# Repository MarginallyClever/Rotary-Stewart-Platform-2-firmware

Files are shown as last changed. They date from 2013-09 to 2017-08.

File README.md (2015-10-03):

#RotaryStewartPlatform2

a 6-axis motion control platform for scientists, students, and enthusiasts.

This project contains the firmware that lives in the brain of a RUMBA board, an Arduino-compatible 6 stepper driver.

This robot is easily controlled from Evil Overlord (https://github.com/i-make-robots/Evil-Overlord), a 3D simulator for Marginally Clever robots.

##Get it

Buy one today at http://www.marginallyclever.com/shop/index.php?main_page=product_info&cPath=1&products_id=74

##Put it together

Our helpful website has all the explanation and pictures to guide you along.
http://learn.marginallyclever.com/index.php/Stewart_Platform_2

##Help!

For technical assistance please visit our forums at https://marginallyclever.com/forums

##More

This code is online @ http://www.github.com/MarginallyClever/RotaryStewartPlatform2

##Author

http://marginallyclever.com
Dan Royer
2013-09-18

This document last updated 2015-10-03

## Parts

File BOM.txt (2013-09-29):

Bill of Materials 2013-09-16 Adafruit Shields
---------------------------------------------
1x Arduino
3x Adafruit Motor Shield v2
6x NEMA17 400 steps per turn
1x USB cable, A to B, 1.5m
1x 12v2a power supply
3x Power cable, 5.5x2.1 1 female to 3 male 
1x Power cable, 5.5x2.1 female
6x micro switches
1x set laser cut parts
6x M3x105 threaded rod
6x M3x5 pan phillips screw
18x M3x15 pan phillips screws
18x M3 hex nuts
12x Traxxas ball joints
10x 2x60 zip ties 

Bill of Materials 2013-09-20 RUMBA shields
---------------------------------------------
1x RUMBA controller
6x NEMA17 400 steps per turn
1x USB cable, A to mini, 1.5m
1x 12v2a power supply
1x Power cable, 5.5x2.1 female
6x micro switches
1x set laser cut parts
6x M3x105 threaded rod
6x M3x5 pan phillips screw
18x M3x15 pan phillips screws
18x M3 hex nuts
12x Traxxas ball joints
10x 2x60 zip ties

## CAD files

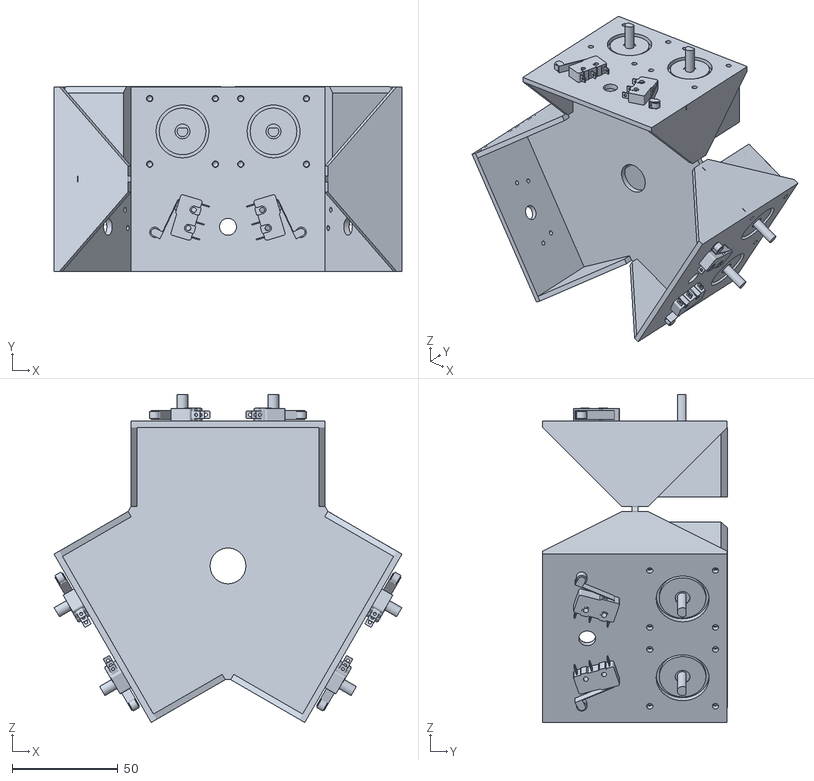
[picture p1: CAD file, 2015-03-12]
base.STL
164.3 x 87.3 x 154.9

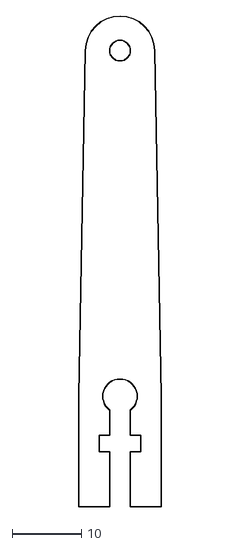
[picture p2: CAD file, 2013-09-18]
DXF files/arm-a.DXF
12.0 x 71.0

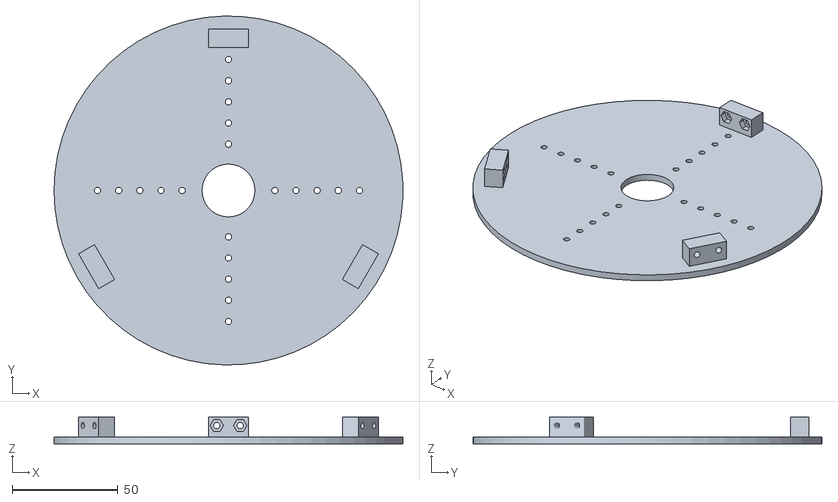
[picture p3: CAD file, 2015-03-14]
STL files/top.STL
165.0 x 164.9 x 12.7

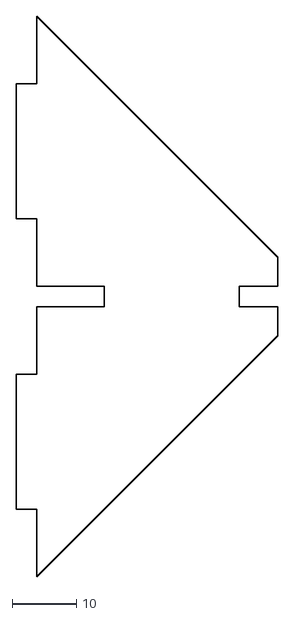
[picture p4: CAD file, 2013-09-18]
DXF files/motor-face-b.DXF
40.7 x 87.2

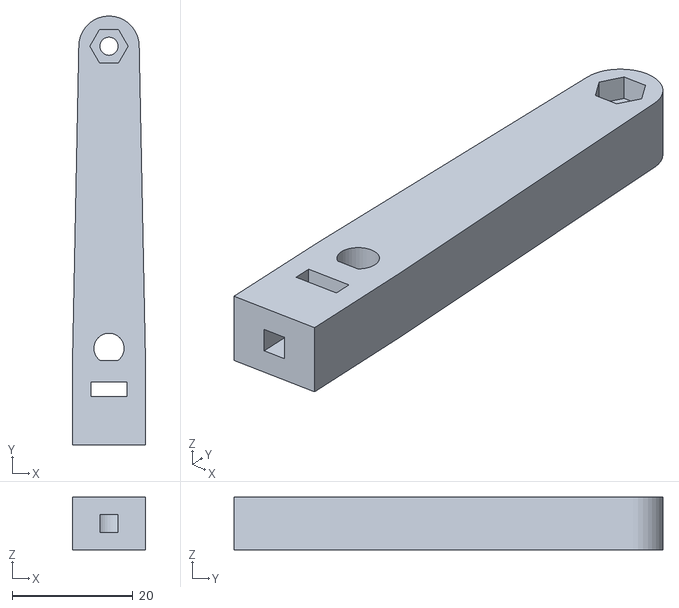
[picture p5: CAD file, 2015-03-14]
STL files/arm.STL
12.0 x 71.0 x 8.70

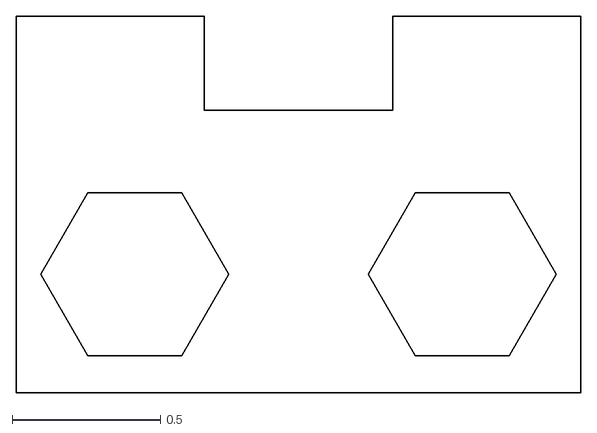
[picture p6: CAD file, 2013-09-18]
DXF files/top-tab-b.DXF
1.91 x 1.27

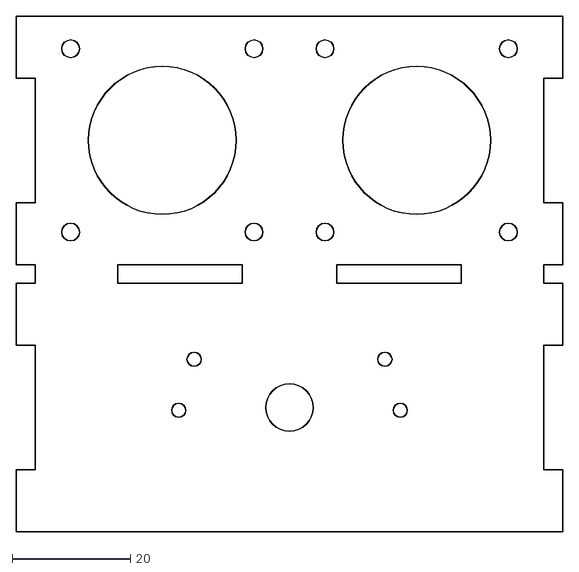
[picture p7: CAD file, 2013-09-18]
DXF files/motor-face-a.DXF
92.3 x 87.2

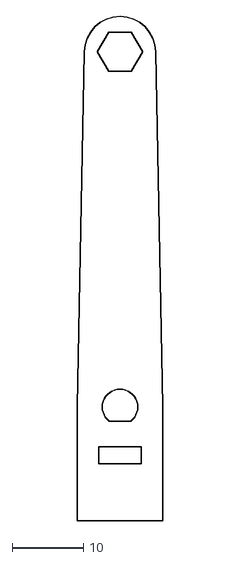
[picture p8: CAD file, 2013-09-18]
DXF files/arm-c.DXF
12.0 x 71.0

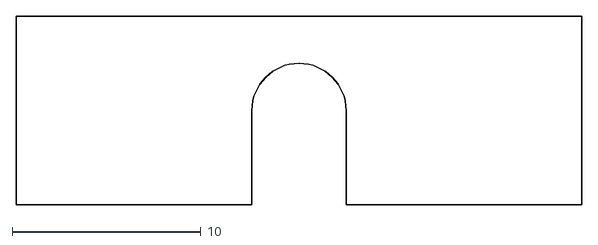
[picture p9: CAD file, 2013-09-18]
DXF files/spacer.DXF
30.0 x 10.0

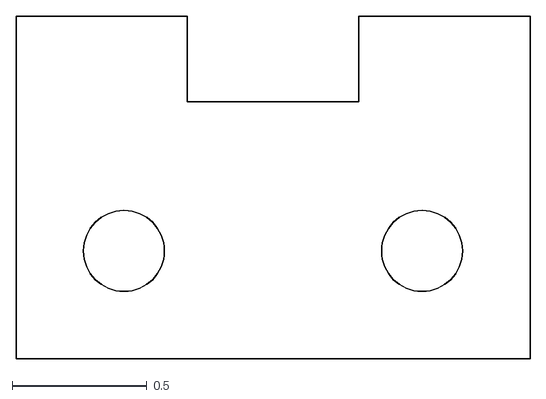
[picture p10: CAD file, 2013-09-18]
DXF files/top-tab-a.DXF
1.91 x 1.27

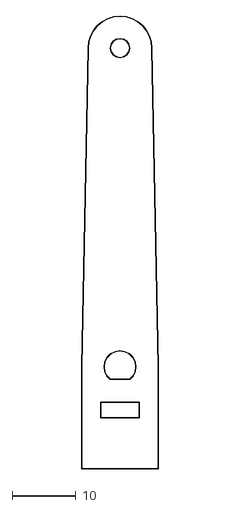
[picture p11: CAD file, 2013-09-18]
DXF files/arm-b.DXF
12.0 x 71.0

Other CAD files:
DXF files/base.DXF
DXF files/top.DXF

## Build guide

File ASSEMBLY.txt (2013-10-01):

Stewart Platform Assembly
---------------------------
Introduction
Glueing
The switches
The stepper motors
The arms
The stewart platform
Final tests

---------------------------
Introduction
	tools you will need
	  	- soldering iron
	  	- Arduino software
	  	- small Phillips screwdriver
	  	- crazy glue
	  	- masking tape
      - pliers
	open and inspect your kit
		IMG_5941
	  	compare with the BOM to make sure everything arrived in working order.
  		We have checked contents before shipping.
      
---------------------------
Glueing
	the frame
		IMG_5944-IMG_5947
	the top
		IMG_5948,49,58-63
	the biceps
		IMG_5950-57
		This is the hardest part!  Make sure the pieces line up correctly.
		Once the glue has dried an M3x15 goes in the hole at the square end and is held in place with an M3 nut.
    
---------------------------
The switches
	soldering
		<picture missing>
		red is the pin closest to the roller.
		black is the center pin.
		blue is the pin closest to the clicker.
	test
		<picture of soldering>
		connect the RUMBA controller to your computer with the USB cable provided.
		<picture of RUMBA input pins>
		connect the switch to an input.
		install test_switches.ino
		open the serial window and set the baud rate to 57600.
		press the switch.  A column should change from 1 to 0.
		disconnect USB.
	install
		thread the wire for two switches through the hole in each face.  secure the switches with zip ties so that the roller is downward.
			<picture>
			Switches 1 and 2 should be side-by-side.
			Switches 3 and 4 should be side-by-side.
			Switches 5 and 6 should be side-by-side.
	test 2
		connect the RUMBA controller to your computer with the USB cable provided.
		the switches again to be sure they are in the correct order.
		disconnect USB.
    
---------------------------
The stepper motors
	attach
		<picture of wiring for stepper 0>
		the wires order from left to right should be red, green, blue, yellow.
		connect the 5.1x2.2 female power supply to the RUMBA
	test one
		connect the 12v2a power supply to the RUMBA.
		install test_steppers_rumba.ino.  Motors will begin to move as soon as sketch uploads.
		open the serial window to see what the code is doing.
		when the test works, remove the stepper from the Arduino.
		disconnect 12v power and USB.
	install
		<picture of tape with writing>
		put a piece of tape on each stepper and at the far end of the wire.
		write the stepper number on the appropriate tape.
		<picture of steppers installed>
		install the steppers in a clockwise order.
			Steppers 1 and 2 should be side-by-side.
			Stepper 1 should be above switch 1.
			Stepper 2 should be above switch 2.
			Repeat for steppers 3-6.
		put the wires through the hole in the center of the frame.
		attach the steppers in order with M3x5 screws.
			The tape will make it easy to keep them organized.
	test 
		Make sure 12v power is not connected.
		put a small piece of tape on each motor shaft so you can easily see it move.
		install firmware_rumba_minimal.ino
		open the serial window.
			G00 X100; should turn stepper 1.
			G00 Y100; should turn stepper 2 *in the opposite direction*.
			G00 Z100; should turn stepper 3 same direction as #1.
			G00 U100; should turn stepper 4 same direction as #2.
			G00 V100; should turn stepper 5 same direction as #1.
			G00 W100; should turn stepper 6 same direction as #2.
      
---------------------------
The arms
  assemble the forearms: One ball joint goes on the end of each threaded rod.
    There should be ~140mm of visible rod between the two ball joints.
    The distance from center hole to center hole should be 167.5mm.
    The holes on the rods should be aligned.
    Use a small pair of pliers to press the metal ball into the plastic frame.
	attach the biceps to the forearms
		<picture of biceps and forearms>
	attach the forearms to the top
		<picture of forearms and top>
		make sure the arms are attached on the correct side. 
	attach the biceps to the motor shafts
		IMG_5964-66
		use the spacer to make sure the biceps are at the correct distance from the frame.
		make sure the biceps are facing the correct direction.
		make sure the biceps touch the limit switches.
    
---------------------------
The stewart platform
	Make sure 12v power is not connected.
	install firmware_rumba_minimal.ino
	open the serial window.
	Connect 12v power.
  
---------------------------
Final tests
	M18; disables power to all stepper motors.
		You can freely move the platform.  Don't forget gravity is in effect!
	M17; enables power to all stepper motors.
		Try manually holding the platform at a strange angle and enabling power.
	Test short movements on each stepper motor.
		M18;
		move the platform so each bicep is approximately level.
		M17;
		Be prepared to disconnect 12v power if something goes wrong.
		G00 F200 Z1; should slowly move the platform up one centimeter.
	test homing
		G28;
		Steppers should immediately move "down" to touch switches and then move to home position.
		Because of the previous F200 they will move slowly.
	test full speed
		G00 F800; changes speed without moving.
		G00 X1.5; should move 15mm sideways.
		G00 Y1.5; should move 15mm orthogonal to X and Z.
		G00 U10; tilt 10 degrees around Y.
		G00 V-8.25; tilt 8.25 degrees around X.
		G00 W5; twist 5 degrees around Z.
		G00 X0 Y0 Z0 U0 V0 W0; will move back to center, flat.
		
Congratulations!  Your platform is assembled and appears to be working.

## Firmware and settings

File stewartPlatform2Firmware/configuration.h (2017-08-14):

#ifndef CONFIGURATION_H
#define CONFIGURATION_H
//------------------------------------------------------------------------------
// Stewart Platform v2 - Supports RUMBA 6-axis motor shield
// dan@marginallycelver.com 2013-09-20
//------------------------------------------------------------------------------
// Copyright at end of file.
// please see http://www.github.com/MarginallyClever/RotaryStewartPlatform2 for more information.


//------------------------------------------------------------------------------
// CONSTANTS
//------------------------------------------------------------------------------
#define VERBOSE              (0)  // increase this number to get more output
#define DEBUG_SWITCHES       (0)

// uncomment this line to test stepper motor wiring
//#define TEST_STEPPERS

// Comms
#define BAUD                 (57600)  // How fast is the Arduino talking?
#define MAX_BUF              (64)  // What is the longest message we can store?

// Stepper motors
#define STEPS_PER_TURN       (400)  // depends on your stepper motor.  most are 200.
#define MICROSTEPS           (16.0)
#define MICROSTEPS_PER_TURN  (STEPS_PER_TURN*MICROSTEPS)
#define MICROSTEP_PER_DEGREE (MICROSTEPS_PER_TURN/360.0)

// speed and acceleration
#define MAX_FEEDRATE         (9000.0)  // depends on timer interrupt & hardware
#define MIN_FEEDRATE         (1.0)
#define DEFAULT_FEEDRATE     (5000.0)
#define DEFAULT_ACCELERATION (3000.0)

#define MIN_STEP_DELAY       (50)  // used for stepper test

// misc
#define NUM_AXIES            (6)

// related to number of instructions that can be buffered.  must be a power of two > 1.
#define MAX_SEGMENTS         (32)  // must be a power of 2
// for splitting lines and look-ahead
#define MM_PER_SEGMENT       (3)

// convenience macros
#define TWOPI                (PI*2.0)
#define DEG2RAD              (PI/180.0)
#define RAD2DEG              (180.0/PI)



//------------------------------------------------------------------------------
// TIMER 
//------------------------------------------------------------------------------
// time passed with no instruction?  Make sure PC knows we are waiting.
#define TIMEOUT_OK           (1000)
// timing
#define CLOCK_FREQ           (16000000L)
#define MAX_COUNTER          (65536L)


// optimize code, please
#define FORCE_INLINE         __attribute__((always_inline)) inline

#ifndef CRITICAL_SECTION_START
  #define CRITICAL_SECTION_START  unsigned char _sreg = SREG;  cli();
  #define CRITICAL_SECTION_END    SREG = _sreg;
#endif //CRITICAL_SECTION_START



//------------------------------------------------------------------------------
// hardware/software pins
//------------------------------------------------------------------------------
#define MOTOR_0_DIR_PIN    (16)
#define MOTOR_0_STEP_PIN   (17)
#define MOTOR_0_ENABLE_PIN (48)
#define MOTOR_0_LIMIT_PIN  (37)

#define MOTOR_1_DIR_PIN    (47)
#define MOTOR_1_STEP_PIN   (54)
#define MOTOR_1_ENABLE_PIN (55)
#define MOTOR_1_LIMIT_PIN  (36)

#define MOTOR_2_DIR_PIN    (56)
#define MOTOR_2_STEP_PIN   (57)
#define MOTOR_2_ENABLE_PIN (62)
#define MOTOR_2_LIMIT_PIN  (35)

#define MOTOR_3_DIR_PIN    (22)
#define MOTOR_3_STEP_PIN   (23)
#define MOTOR_3_ENABLE_PIN (27)
#define MOTOR_3_LIMIT_PIN  (34)

#define MOTOR_4_DIR_PIN    (25)
#define MOTOR_4_STEP_PIN   (26)
#define MOTOR_4_ENABLE_PIN (24)
#define MOTOR_4_LIMIT_PIN  (33)

#define MOTOR_5_DIR_PIN    (28)
#define MOTOR_5_STEP_PIN   (29)
#define MOTOR_5_ENABLE_PIN (39)
#define MOTOR_5_LIMIT_PIN  (32)


//------------------------------------------------------------------------------
// EEPROM MEMORY MAP
//------------------------------------------------------------------------------
#define EEPROM_VERSION   2                         // Increment EEPROM_VERSION when adding new variables

#define ADDR_VERSION     0                         // address of the version number (one byte)
#define ADDR_GUID        (ADDR_VERSION+1)          // address of the UUID (long - 4 bytes)

// sensor adjustments
#define ADDR_ANGLE1      (ADDR_GUID  +4)
#define ADDR_ANGLE2      (ADDR_ANGLE1+4)
#define ADDR_ANGLE3      (ADDR_ANGLE2+4)
#define ADDR_ANGLE4      (ADDR_ANGLE3+4)
#define ADDR_ANGLE5      (ADDR_ANGLE4+4)
#define ADDR_ANGLE6      (ADDR_ANGLE5+4)


//------------------------------------------------------------------------------
// GLOBALS
//------------------------------------------------------------------------------
extern long robot_uid;


/**
* This file is part of Stewart Platform v2.
*
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
re details.
*
* You should have received a copy of the GNU General Public License
* along with Stewart Platform v2. If not, see <http://www.gnu.org/licenses/>.
*/
#endif

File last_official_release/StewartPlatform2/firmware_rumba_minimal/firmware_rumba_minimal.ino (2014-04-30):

//------------------------------------------------------------------------------
// Stewart Platform v2 - Supports Adafruit motor shield v2
// dan@marginallycelver.com 2013-09-07
//------------------------------------------------------------------------------
// Copyright at end of file.
// please see http://www.github.com/MarginallyClever/RotaryStewartPlatform2 for more information.

/**
 * top center to wrist hole: X76.35 Y+/-5.53 Z8.7
 * base center to shoulder hole: X80.93 Y+/-21.5 Z78.31
 */

//------------------------------------------------------------------------------
// CONSTANTS
//------------------------------------------------------------------------------
//#define VERBOSE              (1)  // add to get a lot more serial output.
//#define DEBUG_SWITCHES       (1)

#define VERSION              (1)  // firmware version
#define BAUD                 (57600)  // How fast is the Arduino talking?
#define MAX_BUF              (64)  // What is the longest message Arduino can store?
#define STEPS_PER_TURN       (400)  // depends on your stepper motor.  most are 200.
#define MIN_STEP_DELAY       (100)
#define MAX_FEEDRATE         (1000000/MIN_STEP_DELAY)
#define MIN_FEEDRATE         (0.01)
#define NUM_AXIES            (6)
#define MICROSTEP_MUL        (16.0)

// measurements based on computer model of robot
#define BICEP_LENGTH         (5.01)
#define FOREARM_LENGTH       (16.75)
#define CIRCUMFERENCE        (BICEP_LENGTH*PI*2.0)
#define STEP_DISTANCE        ((CIRCUMFERENCE/MICROSTEP_MUL)/STEPS_PER_TURN)


//------------------------------------------------------------------------------
// INCLUDES
//------------------------------------------------------------------------------


//------------------------------------------------------------------------------
// STRUCTS
//------------------------------------------------------------------------------
// for line()
typedef struct {
  long delta;
  long absdelta;
  int dir;
  long over;
} Axis;


typedef struct {
  int motor_step_pin;
  int motor_dir_pin;
  int motor_enable_pin;
  int motor_scale;  // 1 or -1
  int limit_switch_pin;
  int limit_switch_state;  
} Arm;


//------------------------------------------------------------------------------
// GLOBALS
//------------------------------------------------------------------------------
Arm arms[NUM_AXIES];

Axis a[NUM_AXIES];  // for line()
Axis atemp;  // for line()

char buffer[MAX_BUF];  // where we store the message until we get a ';'
int sofar;  // how much is in the buffer

// speeds
float fr=0;  // human version
long step_delay;  // machine version
int step_delay_s;
int step_delay_us;

float px,py,pz,pu,pv,pw;  // position

// settings
char mode_abs=1;  // absolute mode?

#ifdef VERBOSE
char *letter="UVWXYZ";
#endif


//------------------------------------------------------------------------------
// METHODS
//------------------------------------------------------------------------------


/**
 * delay for the appropriate number of microseconds
 * @input ms how many milliseconds to wait
 */
void pause(long ms) {
  delay( step_delay_s );
  delayMicroseconds( step_delay_us );  // delayMicroseconds doesn't work for ms values > ~16k.
}


/**
 * Set the feedrate (speed motors will move)
 * @input nfr the new speed in steps/second
 */
void feedrate(float nfr) {
  if(fr==nfr) return;  // same as last time?  quit now.

  if(nfr>MAX_FEEDRATE) {
    Serial.print(F("New feedrate must be less than "));
    Serial.print(MAX_FEEDRATE);
    Serial.println(F("steps/s."));
    nfr=MAX_FEEDRATE;
  }
  if(nfr<MIN_FEEDRATE) {  // don't allow crazy feed rates
    Serial.print(F("New feedrate must be greater than "));
    Serial.print(MIN_FEEDRATE);
    Serial.println(F("steps/s."));
    nfr=MIN_FEEDRATE;
  }
  step_delay = 1000000.0/nfr;
  step_delay_s  = step_delay / 1000;
  step_delay_us = step_delay % 1000;
  fr=nfr;
}


/**
 * Set the logical position
 * @input npx new position x
 * @input npy new position y
 */
void position(float npx,float npy,float npz,float npu,float npv,float npw) {
  // here is a good place to add sanity tests
  px=npx;
  py=npy;
  pz=npz;
  pu=npu;
  pv=npv;
  pw=npw;
}


/**
 * Move one motor in a given direction
 * @input the motor number [0...6]
 * @input the direction to move 1 for forward, -1 for backward
 **/
void onestep(int motor,int dir) {
#ifdef VERBOSE
  Serial.print(letter[motor]);
#endif
  dir *= arms[motor].motor_scale;
  digitalWrite(arms[motor].motor_dir_pin,dir>0?LOW:HIGH);
  digitalWrite(arms[motor].motor_step_pin,LOW);
  digitalWrite(arms[motor].motor_step_pin,HIGH);
}


/**
 * Grips the power on the motors
 **/
void motor_enable() {
  int i;
  for(i=0;i<NUM_AXIES;++i) {
    digitalWrite(arms[i].motor_enable_pin,LOW);
  }
}


/**
 * Releases the power on the motors
 **/
void motor_disable() {
  int i;
  for(i=0;i<NUM_AXIES;++i) {
    digitalWrite(arms[i].motor_enable_pin,HIGH);
  }
}


/**
 * Uses bresenham's line algorithm to move both motors
 * @input newx the destination x position
 * @input newy the destination y position
 **/
void line(float newx,float newy,float newz,float newu,float newv,float neww) {
  a[0].delta = newx-px;
  a[1].delta = newy-py;
  a[2].delta = newz-pz;
  a[3].delta = newu-pu;
  a[4].delta = newv-pv;
  a[5].delta = neww-pw;
  
  long i,j,maxsteps=0;

  for(i=0;i<NUM_AXIES;++i) {
    a[i].dir = (a[i].delta > 0 ? 1:-1);
    a[i].absdelta = abs(a[i].delta);
    a[i].over=0;
    if(maxsteps<a[i].absdelta) maxsteps=a[i].absdelta;
  }
  
#ifdef VERBOSE
  Serial.println(F("Start >"));
#endif
  
  for(i=0;i<maxsteps;++i) {
    for(j=1;j<NUM_AXIES;++j) {
      a[j].over += a[j].absdelta;
      if(a[j].over >= maxsteps) {
        a[j].over -= maxsteps;
        onestep(j,a[j].dir);
      }
    }
    pause(step_delay);
  }

#ifdef VERBOSE
  Serial.println(F("< Done."));
#endif

  // This does not take into account movements of a fraction of a step.  They will be misreported and lead to error.
  position(newx,newy,newz,newu,newv,neww);
}


/**
 * Look for character /code/ in the buffer and read the float that immediately follows it.
 * @return the value found.  If nothing is found, /val/ is returned.
 * @input code the character to look for.
 * @input val the return value if /code/ is not found.
 **/
float parsenumber(char code,float val) {
  char *ptr=buffer;
  while(ptr && *ptr && ptr<buffer+sofar) {
    if(*ptr==code) {
      return atof(ptr+1);
    }
    ptr=strchr(ptr,' ')+1;
  }
  return val;
} 


/**
 * write a string followed by a float to the serial line.  Convenient for debugging.
 * @input code the string.
 * @input val the float.
 */
void output(char *code,float val) {
  Serial.print(code);
  Serial.println(val);
}


/**
 * print the current position, feedrate, and absolute mode.
 */
void where() {
  output("X",px);
  output("Y",py);
  output("Z",pz);
  output("U",pu);
  output("V",pv);
  output("W",pw);
  output("F",fr);
  Serial.println(mode_abs?"ABS":"REL");
} 


/**
 * display helpful information
 */
void help() {
  Serial.print(F("StewartPlatform v4-2"));
  Serial.println(VERSION);
  Serial.println(F("Commands:"));
  Serial.println(F("M17/M18; - enable/disable motors"));
  Serial.println(F("M100; - this help message"));
  Serial.println(F("M114; - report position and feedrate"));
  Serial.println(F("F, G00, G01, G04, G17, G18, G28, G90, G91, G92 as described by http://en.wikipedia.org/wiki/G-code"));
}


/**
 * Read the input buffer and find any recognized commands.  One G or M command per line.
 */
void processCommand() {
  int cmd = parsenumber('G',-1);
  switch(cmd) {
  case  0: // move linear
  case  1: // move linear
    feedrate(parsenumber('F',fr));
    line( parsenumber('X',(mode_abs?px:0)) + (mode_abs?0:px),
          parsenumber('Y',(mode_abs?py:0)) + (mode_abs?0:py),
          parsenumber('Z',(mode_abs?pz:0)) + (mode_abs?0:pz),
          parsenumber('U',(mode_abs?pu:0)) + (mode_abs?0:pu),
          parsenumber('V',(mode_abs?pv:0)) + (mode_abs?0:pv),
          parsenumber('W',(mode_abs?pw:0)) + (mode_abs?0:pw) );
    break;
  case  4:  pause(parsenumber('P',0)*1000);  break;  // dwell
  case 28:  find_home();  break;  
  case 90:  mode_abs=1;  break;  // absolute mode
  case 91:  mode_abs=0;  break;  // relative mode
  case 92:  // set logical position
    position( parsenumber('X',0),
              parsenumber('Y',0),
              parsenumber('Z',0),
              parsenumber('U',0),
              parsenumber('V',0),
              parsenumber('W',0) );
    break;
  default:  break;
  }

  cmd = parsenumber('M',-1);
  switch(cmd) {
  case 17:  motor_enable();  break;
  case 18:  motor_disable();  break;
  case 100:  help();  break;
  case 114:  where();  break;
  default:  break;
  }
}


/**
 * prepares the input buffer to receive a new message and tells the serial connected device it is ready for more.
 */
void ready() {
  sofar=0;  // clear input buffer
  Serial.print(F(">"));  // signal ready to receive input
}


/**
 * read the limit switch states
 * @return 1 if a switch is being hit
 */
char read_switches() {
  char i, hit=0;
  int state;
  
  for(i=0;i<6;++i) {
    state=digitalRead(arms[i].limit_switch_pin);
#ifdef DEBUG_SWITCHES
    Serial.print(state);
    Serial.print('\t');
#endif
    if(arms[i].limit_switch_state != state) {
      arms[i].limit_switch_state = state;
#ifdef DEBUG_SWITCHES
      Serial.print(F("Switch "));
      Serial.println(i,DEC);
#endif
    }
    if(state == LOW) ++hit;
  }
#ifdef DEBUG_SWITCHES
  Serial.print('\n');
#endif
  return hit;
}


/**
 * setup the limit switches
 */
void setup_switches() {
  arms[0].limit_switch_pin=37;
  arms[1].limit_switch_pin=36;
  arms[2].limit_switch_pin=35;
  arms[3].limit_switch_pin=34;
  arms[4].limit_switch_pin=33;
  arms[5].limit_switch_pin=32;
  
  for(int i=0;i<NUM_AXIES;++i) {  
    // set the switch pin
    arms[i].limit_switch_state=HIGH;
    pinMode(arms[i].limit_switch_pin,INPUT);
    digitalWrite(arms[i].limit_switch_pin,HIGH);
  }
}


/**
 * Move the motors until they connect with the limit switches, then return to "zero" position.
 */
void find_home() {
  char i;
  // until all switches are hit
  while(read_switches()<NUM_AXIES) {
#ifdef VERBOSE
  Serial.println(read_switches(),DEC);
#endif
    // for each stepper,
    for(i=0;i<NUM_AXIES;++i) {
      // if this switch hasn't been hit yet
      if(arms[i].limit_switch_state == HIGH) {
        // move "down"
        onestep(i,-1);
      }
        delay(10);
    }
  }

  // The arms are 19.69 degrees from straight down when they hit the switch.
  // @TODO: This could be better customized in firmware.
  float horizontal = 90.00 - 19.69;
  long steps_to_zero = STEPS_PER_TURN * MICROSTEP_MUL * horizontal / 360.00;
#ifdef VERBOSE
  Serial.print("steps=");
  Serial.println(step_size);
#endif

  for(;steps_to_zero>0;--steps_to_zero) {
    for(i=0;i<NUM_AXIES;++i) {
      onestep(i,1);
    }
        delay(10);
  }
  position(0,0,0,0,0,0);
}


/**
 * setup the motor shields
 */
void setup_shields() {
  arms[0].motor_step_pin=17;
  arms[0].motor_dir_pin=16;
  arms[0].motor_enable_pin=48;

  arms[1].motor_step_pin=54;
  arms[1].motor_dir_pin=47;
  arms[1].motor_enable_pin=55;

  arms[2].motor_step_pin=57;
  arms[2].motor_dir_pin=56;
  arms[2].motor_enable_pin=62;

  arms[3].motor_step_pin=23;
  arms[3].motor_dir_pin=22;
  arms[3].motor_enable_pin=27;

  arms[4].motor_step_pin=26;
  arms[4].motor_dir_pin=25;
  arms[4].motor_enable_pin=24;

  arms[5].motor_step_pin=29;
  arms[5].motor_dir_pin=28;
  arms[5].motor_enable_pin=39;
  
  for(int i=0;i<6;++i) {  
    // set the motor pin & scale
    arms[i].motor_scale=((i%2)? -1:1);
    pinMode(arms[i].motor_step_pin,OUTPUT);
    pinMode(arms[i].motor_dir_pin,OUTPUT);
    pinMode(arms[i].motor_enable_pin,OUTPUT);
  }
}


/**
 * First thing this machine does on startup.  Runs only once.
 */
void setup() {
  Serial.begin(BAUD);  // open coms
  help();  // say hello

  setup_shields();
  setup_switches();
  feedrate(6400);  // set default speed
  motor_enable();
  position(0,0,0,0,0,0);
  
  ready();
}


/**
 * After setup() this machine will repeat loop() forever.
 */
void loop() {
  // listen for serial commands
  while(Serial.available() > 0) {  // if something is available
    char c=Serial.read();  // get it
    Serial.print(c);  // repeat it back so I know you got the message
    if(sofar<MAX_BUF) buffer[sofar++]=c;  // store it
    if(buffer[sofar-1]==';') break;  // entire message received
  }

  if(sofar>0 && buffer[sofar-1]==';') {
    // we got a message and it ends with a semicolon
    buffer[sofar]=0;  // end the buffer so string functions work right
    Serial.print(F("\r\n"));  // echo a return character for humans
    processCommand();  // do something with the command
    ready();
  }

#ifdef DEBUG_SWITCHES  
  read_switches();
#endif
}


/**
* This file is part of Stewart Platform v2.
*
* Stewart Platform v2 is free software: you can redistribute it and/or modify
* it under the terms of the GNU General Public License as published by
* the Free Software Foundation, either version 3 of the License, or
* (at your option) any later version.
*
* Stewart Platform v2 is distributed in the hope that it will be useful,
* but WITHOUT ANY WARRANTY; without even the implied warranty of
* MERCHANTABILITY or FITNESS FOR A PARTICULAR PURPOSE. See the
* GNU General Public License for more details.
*
* You should have received a copy of the GNU General Public License
* along with Stewart Platform v2. If not, see <http://www.gnu.org/licenses/>.
*/

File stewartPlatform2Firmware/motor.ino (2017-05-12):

//------------------------------------------------------------------------------
// Stewart Platform v2 - Supports RUMBA 6-axis motor shield
// dan@marginallycelver.com 2013-09-20
//------------------------------------------------------------------------------
// Copyright at end of file.
// please see http://www.github.com/MarginallyClever/RotaryStewartPlatform2 for more information.


//------------------------------------------------------------------------------
// GLOBALS
//------------------------------------------------------------------------------

const char *motor_letters = "ABCDE";


//------------------------------------------------------------------------------
// METHODS
//------------------------------------------------------------------------------

void motor_setup() {
  int i;
  
  // set up the pins
  robot.arms[0].motor_step_pin=MOTOR_0_STEP_PIN;
  robot.arms[0].motor_dir_pin=MOTOR_0_DIR_PIN;
  robot.arms[0].motor_enable_pin=MOTOR_0_ENABLE_PIN;
  robot.arms[0].limit_switch_pin=MOTOR_0_LIMIT_PIN;

  robot.arms[1].motor_step_pin=MOTOR_1_STEP_PIN;
  robot.arms[1].motor_dir_pin=MOTOR_1_DIR_PIN;
  robot.arms[1].motor_enable_pin=MOTOR_1_ENABLE_PIN;
  robot.arms[1].limit_switch_pin=MOTOR_1_LIMIT_PIN;
  
  robot.arms[2].motor_step_pin=MOTOR_2_STEP_PIN;
  robot.arms[2].motor_dir_pin=MOTOR_2_DIR_PIN;
  robot.arms[2].motor_enable_pin=MOTOR_2_ENABLE_PIN;
  robot.arms[2].limit_switch_pin=MOTOR_2_LIMIT_PIN;
  
  robot.arms[3].motor_step_pin=MOTOR_3_STEP_PIN;
  robot.arms[3].motor_dir_pin=MOTOR_3_DIR_PIN;
  robot.arms[3].motor_enable_pin=MOTOR_3_ENABLE_PIN;
  robot.arms[3].limit_switch_pin=MOTOR_3_LIMIT_PIN;
  
  robot.arms[4].motor_step_pin=MOTOR_4_STEP_PIN;
  robot.arms[4].motor_dir_pin=MOTOR_4_DIR_PIN;
  robot.arms[4].motor_enable_pin=MOTOR_4_ENABLE_PIN;
  robot.arms[4].limit_switch_pin=MOTOR_4_LIMIT_PIN;
  
  robot.arms[5].motor_step_pin=MOTOR_5_STEP_PIN;
  robot.arms[5].motor_dir_pin=MOTOR_5_DIR_PIN;
  robot.arms[5].motor_enable_pin=MOTOR_5_ENABLE_PIN;
  robot.arms[5].limit_switch_pin=MOTOR_5_LIMIT_PIN;
  
  for(i=0;i<NUM_AXIES;++i) {  
    // set the motor pin & scale
    robot.arms[i].motor_scale=((i%2)? -1:1);
    pinMode(robot.arms[i].motor_step_pin,OUTPUT);
    pinMode(robot.arms[i].motor_dir_pin,OUTPUT);
    pinMode(robot.arms[i].motor_enable_pin,OUTPUT);
    // set the switch pin
    robot.arms[i].limit_switch_state=HIGH;
    pinMode(robot.arms[i].limit_switch_pin,INPUT);
    digitalWrite(robot.arms[i].limit_switch_pin,HIGH);
  }
}


void motor_segment(float new_feed_rate) {
  int i;
  // convert angle to motor steps
  for(i=0;i<NUM_AXIES;++i) {
    robot.arms[i].new_step = robot.arms[i].angle * MICROSTEP_PER_DEGREE;
  }

#if VERBOSE > 0
  Serial.print(robot.arms[0].new_step);  Serial.print(" ");
  Serial.print(robot.arms[1].new_step);  Serial.print(" ");
  Serial.print(robot.arms[2].new_step);  Serial.print(" ");
  Serial.print(robot.arms[3].new_step);  Serial.print(" ");
  Serial.print(robot.arms[4].new_step);  Serial.print(" ");
  Serial.print(robot.arms[5].new_step);  Serial.print("\n");
#endif

  motor_prepare_segment(robot.arms[0].new_step,
                        robot.arms[1].new_step,
                        robot.arms[2].new_step,
                        robot.arms[3].new_step,
                        robot.arms[4].new_step,
                        robot.arms[5].new_step,new_feed_rate);
}


/**
 * Grips the power on the motors
 **/
void motor_enable() {
  int i;
  for(i=0;i<NUM_AXIES;++i) {
    digitalWrite(robot.arms[i].motor_enable_pin,LOW);
  }
}


/**
 * Releases the power on the motors
 **/
void motor_disable() {
  int i;
  for(i=0;i<NUM_AXIES;++i) {
    digitalWrite(robot.arms[i].motor_enable_pin,HIGH);
  }
}


/**
 * print the current motor positions in steps
 */
void motor_where() {
  output("0",robot.arms[0].new_step);
  output("1",robot.arms[1].new_step);
  output("2",robot.arms[2].new_step);
  output("3",robot.arms[3].new_step);
  output("4",robot.arms[4].new_step);
  output("5",robot.arms[5].new_step);
}


/**
 * test one motor by moving it forward and back
 */
void move_motor(int i) {
  int j;
  
  Serial.print("  forward ");
  Serial.println(i);

  digitalWrite(robot.arms[i].motor_dir_pin,HIGH);
  for(j=0;j<MICROSTEPS_PER_TURN;++j) {
    digitalWrite(robot.arms[i].motor_step_pin,HIGH);
    digitalWrite(robot.arms[i].motor_step_pin,LOW);
    delayMicroseconds(MIN_STEP_DELAY);
  }

  Serial.print("  backward ");
  Serial.println(i);

  digitalWrite(robot.arms[i].motor_dir_pin,LOW);
  for(j=0;j<MICROSTEPS_PER_TURN;++j) {
    digitalWrite(robot.arms[i].motor_step_pin,HIGH);
    digitalWrite(robot.arms[i].motor_step_pin,LOW);
    delayMicroseconds(MIN_STEP_DELAY);
  }
}

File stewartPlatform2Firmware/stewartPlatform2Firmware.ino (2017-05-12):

//------------------------------------------------------------------------------
// Stewart Platform v2 - Supports RUMBA 6-axis motor shield
// dan@marginallycelver.com 2013-09-20
// First time you run the robot send R70 and R71 to initialize the motor angles.
//------------------------------------------------------------------------------
// Copyright at end of file.
// please see http://www.github.com/MarginallyClever/RotaryStewartPlatform2 for more information.


//------------------------------------------------------------------------------
// INCLUDES
//------------------------------------------------------------------------------
#include "configuration.h"
#include "vector3.h"
#include "segment.h"
#include "hexapod.h"


//------------------------------------------------------------------------------
// GLOBALS
//------------------------------------------------------------------------------
// speeds
float feed_rate = DEFAULT_FEEDRATE; // how fast the EE moves in cm/s
float acceleration = DEFAULT_ACCELERATION;

// settings
char mode_abs = 1; // absolute mode?

// misc
long robot_uid = 0;

//------------------------------------------------------------------------------
// METHODS
//------------------------------------------------------------------------------
/**
    finds angle of dy/dx as a value from 0...2PI
    @return the angle
*/
float atan3(float dy, float dx) {
  float a = atan2(dy, dx);
  if (a < 0) a = (PI * 2.0) + a;
  return a;
}


/**
   Delay for the appropriate time. delayMicroseconds() doesn't work for ms values > ~16k.
   @input us how many microseconds to wait
*/
void pause(long us) {
  delay(us / 1000);
  delayMicroseconds(us % 1000);
}


/**
   Set the feedrate (speed motors will move)
   @input nfr the new speed in steps/second
*/
float feedrate(float nfr) {
  if (feed_rate == nfr) return nfr; // same as last time?  quit now.

  if (nfr > MAX_FEEDRATE) {
    Serial.print(F("Feedrate set to maximum ("));
    Serial.print(MAX_FEEDRATE);
    Serial.println(F("steps/s)"));
    nfr = MAX_FEEDRATE;
  }
  if (nfr < MIN_FEEDRATE) { // don't allow crazy feed rates
    Serial.print(F("Feedrate set to minimum ("));
    Serial.print(MIN_FEEDRATE);
    Serial.println(F("steps/s)"));
    nfr = MIN_FEEDRATE;
  }
  feed_rate = nfr;

  return feed_rate;
}


/**
   display helpful information
*/
void help() {
  Serial.print(F("\n\nHELLO WORLD! I AM STEWART PLATFORM V4.2 #"));
  Serial.println(robot_uid, DEC);
  sayVersionNumber();
  Serial.println(F("== http://www.marginallyclever.com/ =="));
  Serial.println(F("I understand the following commands:"));
  Serial.println(F("Nx [A]*y (this is line number x, with checksum y)\n"\
                   "Where A is one of the following:\n"\
                   "G0 [Xx] [Yy] [Zz] (move to XYZ)\n"\
                   "G1 [Xx] [Yy] [Zz] (move to XYZ)\n"\
                   "G2 [Xx] [Yy] [Zz] (move anticlockwise in XY plane to XYZ)\n"\
                   "G3 [Xx] [Yy] [Zz] (move clockwise in XY plane to to XYZ)\n"\
                   "G4 [Pp] [Ss] (wait P seconds and S milliseconds)\n"\
                   "G28 (find home)\n"\
                   "G54-59 [Xx] [Yy] [Zz] (adjust tool offset)\n"\
                   "G90 (absolute movement mode)\n"\
                   "G91 (relative movement mode)\n"\
                   "M17 (disable motors)\n"\
                   "M18 (enable motors)\n"\
                   "M100 (help)\n"\
                   "M110 N* (set line number to *)\n"\
                   "M114 (where)\n"\
                   "UID * (write robot UID * to EEPROM)\n"\
                   "R60 [Aa] [Bb] [Cc] [Dd] [Ed] (set sensors adjustment to new value [abcde])\n"\
                   "R61 (display switch adjustment)\n"\
                   "R70 (write sensor adjustments to memory)\n"\
                   "R71 (reset switch adjustmentles to factory default)\n"));
  // See hexapod_position() for note about why G92 is removed
}


void sayVersionNumber() {
  char versionNumber = loadVersion();

  Serial.print(F("Firmware v"));
  Serial.println(versionNumber, DEC);
}


/**
   First thing this machine does on startup.  Runs only once.
*/
void setup() {
  loadConfig();

  Serial.begin(BAUD);  // open coms

  motor_setup();
  segment_setup();

  hexapod_setup();
  feedrate(DEFAULT_FEEDRATE);  // set default speed

  help();  // say hello
  parser_ready();
}


/**
   After setup() this machine will repeat loop() forever.
*/
void loop() {
#ifdef TEST_STEPPERS
  int i=0;

  for(i=0;i<6;++i) {
    Serial.print("motor ");
    Serial.println(i);
    move_motor(i);
  }

#endif
#ifdef TEST_SWITCHES
  for(int i=0;i<NUM_SWITCHES;++i) {
    int j=robot.arms[i].limit_switch_pin;
    int state=digitalRead(j);
    Serial.print(state?'1':'0');
    Serial.print('\t');
  }
  Serial.println();
  delay(50);
#endif
  
  parser_listen();
}


/**
  This file is part of Stewart Platform v2.

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
NU General Public License as published by
  the Free Software Foundation, either version 3 of the License, or
  (at your option) any later version.

  Stewart Platform v2 is distributed in the hope that it will be useful,
  but WITHOUT ANY WARRANTY; without even the implied warranty of
  MERCHANTABILITY or FITNESS FOR A PARTICULAR PURPOSE. See the
  GNU General Public License for more details.

  You should have received a copy of the GNU General Public License
  along with Stewart Platform v2. If not, see <http://www.gnu.org/licenses/>.
*/

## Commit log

2013-09-18 Revert "initial commit"
    This reverts commit c0bb3e7f41a3a6736d664b5d8bb628a06988f7d5.
    [arm-a.DXF, arm-b.DXF, arm-c.DXF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]
2013-09-18 1
    added readme, license, bill of materials, dxf files, and arduino
    sketches
    [arm-a.DXF, arm-b.DXF, arm-c.DXF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]
2013-09-21 2
    - added firmware for rumba
    - added sketches to test during assembly
2013-09-22 3
    - separated Adafruit Motor Shield BOM and RUMBA BOM
    - added high-level XYZ (translate) and UVW (roll,pitch,yaw) code.
    - no sanity checks on movement! be careful.
    - removed G92. See hexapod_position() for explanation.
2013-09-22 4
    - corrected legal notice
    - corrected github URL
    - divided firmware_rumba.ino into files by logical grouping
    [configuration.h]
2013-09-22 5
    - fixed segment system from last commit, smooths single movements.
    - ground work laid for moving on one thread, queueing on another.
    [firmware_rumba.ino, hexapod.ino, segment.ino]
2013-09-23 6
    - optimized steps within motor_move_segment()
    - moved a few things to be more consistent
2013-09-24 7
    - added ASSEMBLY.txt with instructions
    - commented out hexapod_find_home() in setup(). Add it back in when
    you are confident your machine works.
    - renamed test_switches_ams2 to test_switches (it is agnostic)
2013-09-29 8
    - added TOC to ASSEMBLY.txt
    - added forearm assembly to ASSEMBLY.txt
2013-10-01 8
    - reduced max steps for calculations, reduces inter-command delay
    - defined out some VERBOSE stuff, reduces inter-command delay
    - added pliers to ASSEMBLY.txt
2013-10-08 9
    Added some assembly pictures. Needs more!
2013-10-09 10
    - added more assembly pictures
    - changed assembly document to html
    - includes adafruit motor shield 2 firmware
2013-11-01 10.1
    Special thanks to Aaron Isaacs for this update.
    - corrected the pin numbers in test_switches_rumba.ino
    - moved an assembly instruction to make more sense
    - removed remaining Adafruit references
    -
    [configuration.h]
2013-11-02 10.3
    - Improved assembly instructions with suggestions from Aaron Isaacs.
    - set a consistent MIN_STEP_DELAY across each firmware
    [configuration.h]
2013-11-04 11
    Added timer interrupt for smoother motion control
    [configuration.h]
2013-11-06 11.1
    - moved timer start (on first segment) from hexapod.ino to segment.ino.
2013-11-21 11.1
    Updated assembly instructions.
    - improved Arduino steps
    - added motor extension descriptions.
    - added screen.css to standardize look & feel.
2013-11-22 11.2
    - added more pictures to ASSEMBLY document
2014-01-05 12
    moved assembly steps to
    http://learn.marginallyclever.com/index.php/Stewart_Platform_2
2014-04-30 13
    - optimized timer1 inner loop for smoother motion
    [configuration.h]
2014-05-02 - added G54…G59 tool offsets (untested) - added G2 & G3 (arcs in XY plane)
    [configuration.h]
2014-05-02 15
    - fixed G4 (dwell)
    [firmware_rumba.ino, parser.ino]
2014-09-13 16
    - added acceleration
    - added G92
    - improved support for multiple tools
    [configuration.h]
2014-10-15 18
    - fixed test_steppers_rumba (was only turning one of the six steppers)
    [test_steppers_rumba.ino]
2015-03-12 added STL files
    [arm.STL, base.STL, top.STL]
2015-03-14 matched visuals and equations
    Matched the simulation of the robot to the look of the robot. Should
    now be 1:1.
    [arm.STL, configuration.h, top.STL]
2015-03-14 added motion and angle limits
    [configuration.h]
2015-06-08 fixed speeds over 10k
    speeds 10001-20000 were 2x the number of steps
    speeds 20000+ were 4x.
    Fixed.
    [segment.ino]
2015-06-09 added accel/decel from Makelangelo
    should allow faster top speeds
    [configuration.h]
2015-10-03 Added GUID to EEPROM like all MC robots
    [configuration.h]
2015-10-03 removed outdated Java stuff
    Project is now exclusively the RSP2 firmware.
    [arm.STL, configuration.h, top.STL]
2015-11-03 possible fix for #1
    FK positions were remembered while IK positions were being forgotten.
    This should fix it to prevent unexpected move between positions.
    [firmware_rumba.ino, hexapod.ino]
2016-04-03 changed DEBUG_SWITCHES to make install easier.
    set the define to a non-zero value to see the switches.
    [configuration.h]
2016-04-09 Improved each arm angle now individually stored in EEPROM
    fine-grain correction without firmware tweaking is better.
    [configuration.h]
2016-04-09 tweakable switch angles now adjustable via gcode.
2016-06-02 updating some numbers for better performance.
    [configuration.h]
2016-06-26 fix for bresenham overstep
    [hexapod.ino, segment.ino]
2017-05-12 integrated tests, better filenames
    less confusing in "open recent"
    [configuration.h]
2017-08-14 turn off stepper test
    [configuration.h]
